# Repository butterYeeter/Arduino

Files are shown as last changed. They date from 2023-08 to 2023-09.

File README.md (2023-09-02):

# Robot Documentation

<!-- > Disclaimer! This repo is a fork of the actual repo used so that we could format it nicely -->

## Table of Contents
- [Performance Video](#performance-video)
- [Mobility Management](#mobility-management)
  - [Robot Version 1](#robot-version-1)
  - [Improvements](#improvements)
- [Power and Sense Management](#power-and-sense-management)
  - [Robot Version 1](#robot-version-1-1)
  - [Improvements](#improvements-1)
- [Obstacle Management](#obstacle-management)

### Performance Video
https://github.com/butterYeeter/Arduino/assets/100842250/680a6417-5dfc-4aaf-9352-56b448d2d792

### Mobility Management
#### Robot Version 1
In the first version of the **'robot'**, the **motors were managed by an [Arduino Nano](/docs/nano.pdf)**. We **communicated with board via [I2C](https://en.wikipedia.org/wiki/I%C2%B2C)**. The main board(a [Pi Pico](/docs/pico.pdf)) sent what speed the motors should be run. The **motor speed was controlled via [PWM](https://en.wikipedia.org/wiki/Pulse-width_modulation)**. High torque low rpm motors were used in the beginning however we ran into issues with the complicated belt system used to drive the wheels. 
 
We then **switched to a lower torque but high rpm brushed dc motor** which was **compatible with an 'off the shelf' gear box**. The motor was also run at a higher than recomended voltage and was **wired with capicitors to reduce EMF**(Which was causing our gyro control board to reset). Steering was handled using another **pi pico with a gyro sensor attached**. This board **controlled a servo using PWM** which controlled the steering rack. The main board communicated(via I2C) the target angle the gyro board should maintain using the steering rack.

The **old chasis** was a combination of 3D printing and hand cut MDF board. The model was a modification(done in Fusion 360) of a base design provided to us by our club. All the control boards as well as the the motor, gear box, servo, gyro, battery and boost converters were **mounted to this chasis**. The TOF sensors used for naviation were mounted to an **mdf frame**(which was connected to the chasis). [Model available here](https://github.com/butterYeeter/Arduino/blob/main/models/body_v2.stl)

<p>
    The drive motor
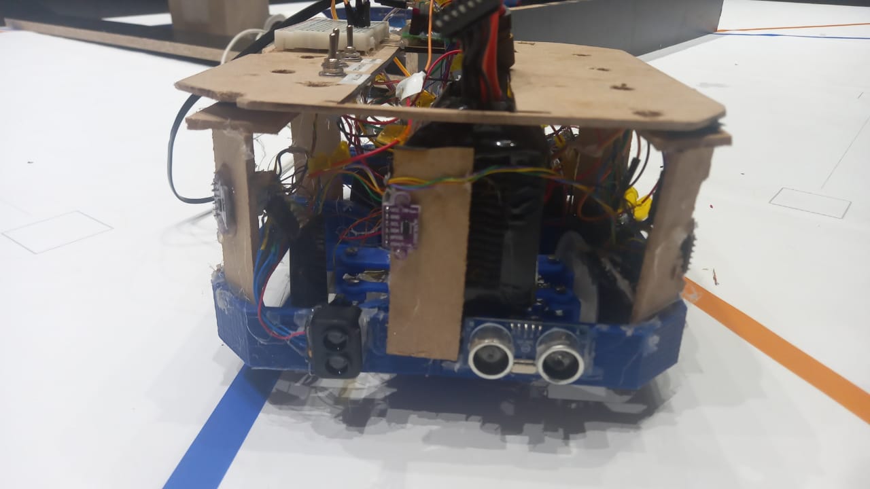
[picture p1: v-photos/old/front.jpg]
Meet Chihuahua! Our lovely, crazy robot :P
    
</p>

#### Improvements
After the provintial round of the competition, a major decision was made to completely redesign the robot. A new chasis was designed(available ```[here](/models/body_v2.stl)```) and is **completely 3D printed**. This helped improve on the flimsy nature of the old MDF frame. **Components** of the old design was **reused** such as the servo for steering as well as the gearbox. The chasis consists of an **interior chasis for mounting components**, steering rack and motors and an **exterior chasis that acts as a bumper**. 

A choice was made to use **2 drive motors**(connected to the same axle) for **increased torque**(initially a decision was made to ram into the walls according to which traffic sign is seen by the camera). Previously **8 [Time of Flight](/docs/tof.pdf) sensors was used** however we then **switched to one fancy 360 degrees scanning lidar**. This is mounted in the center of the chasis and **no other components sit above it to prevent inteference with the measurements**. On top of the lidar, a **```pixy cam``` is mounted on a servo to scan for traffic signs**.

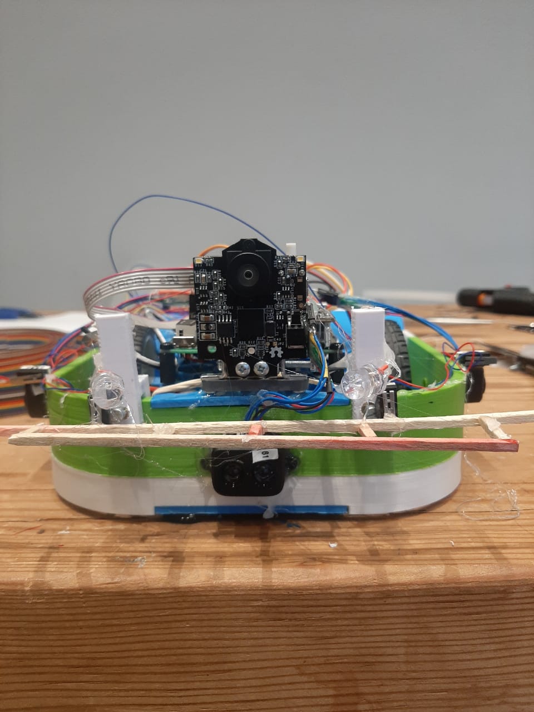
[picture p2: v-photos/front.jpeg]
Meet chihuahua mk3


### Power and Sense Management
#### Robot Version 1
The first version of the robot was **powered** using a **3 cell Li-PO battery** however we ran into **issues**. We then **tested using a 2 cell Li-PO** however the **voltage drop** was too great and their were **capacity issues**.  We ulitmately switched to a **6 cell battery in combination with voltage regulators**. 

A variety of sensors were used in this first robot for the challenges. 8 **[Time of Flight](/docs/tof.pdf)** sensors(and one fancy one) as well as a **[BMP 180](/docs/bmp180.pdf)**(the old gyro). These were **managed by 2 [Rasberry Pi Pico's](/docs/pico.pdf)**, one for managing the Time of Flight sensors and one for managing the gyro(BMP 180). The **time of flight sensors detected the distance from the walls** from all sides of the car. The **main board would then request the sensor data** from the Time of Flight board. The gyro board simply used the **BMP 180's output for driving straight** consistently and would accept a **target angle to follow from the main board**.

#### Improvements
The new robot is **powered by a 4 cell battery due to new the chasis**. The previous **6 cell would not fit** within the allocated space on the chasis so we used the **smaller 4 cell**. The 8 time of flight sensors as well as the one fancy time of flight were **discarded in favour of a 360 degree scanning lidar**. The old sensors had a bad field of view and would throw false positives as to what the actual distance reading was. This caused major issues when it came to reliablity of the function of the car. The new lidar has an **excellent field of view of just 2 degrees** and can measure distances of up to 12 meters. This has greatly reduced errors that were associated to the time of flight sensors. We still use a **Pi Pico for managing** this sensor. The sensor uses a basic **one wire serial interface**. Unfortunately there were further issues with dynamic memory allocation as we had to port a library from the Raspberry Pi 4B to the Pi Pico. We finally on 3 good time of flight sensor which are reliable. 

<p align=center>
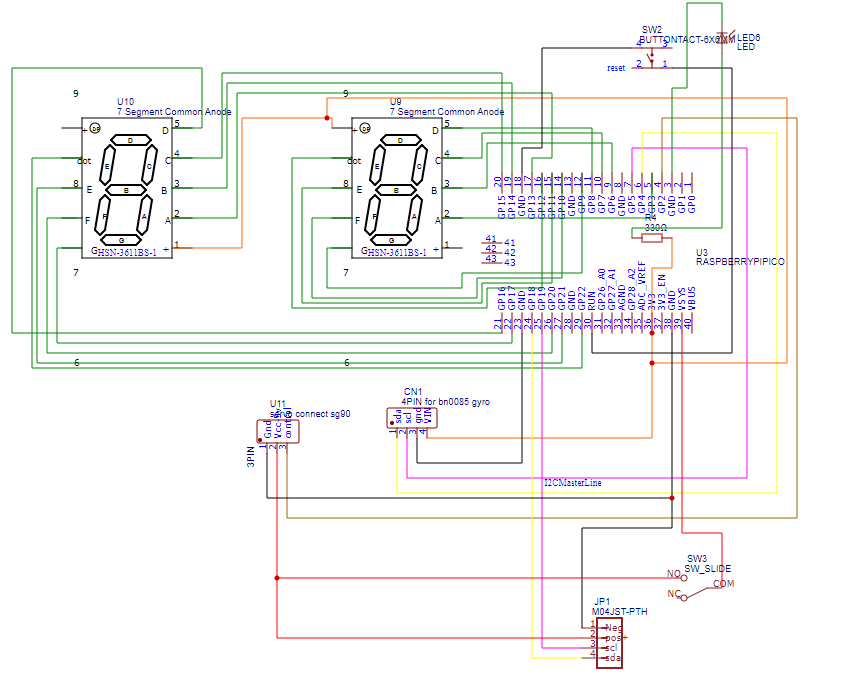
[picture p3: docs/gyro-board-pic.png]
Main Board and LIDAR
  
</p>
<p align=center>
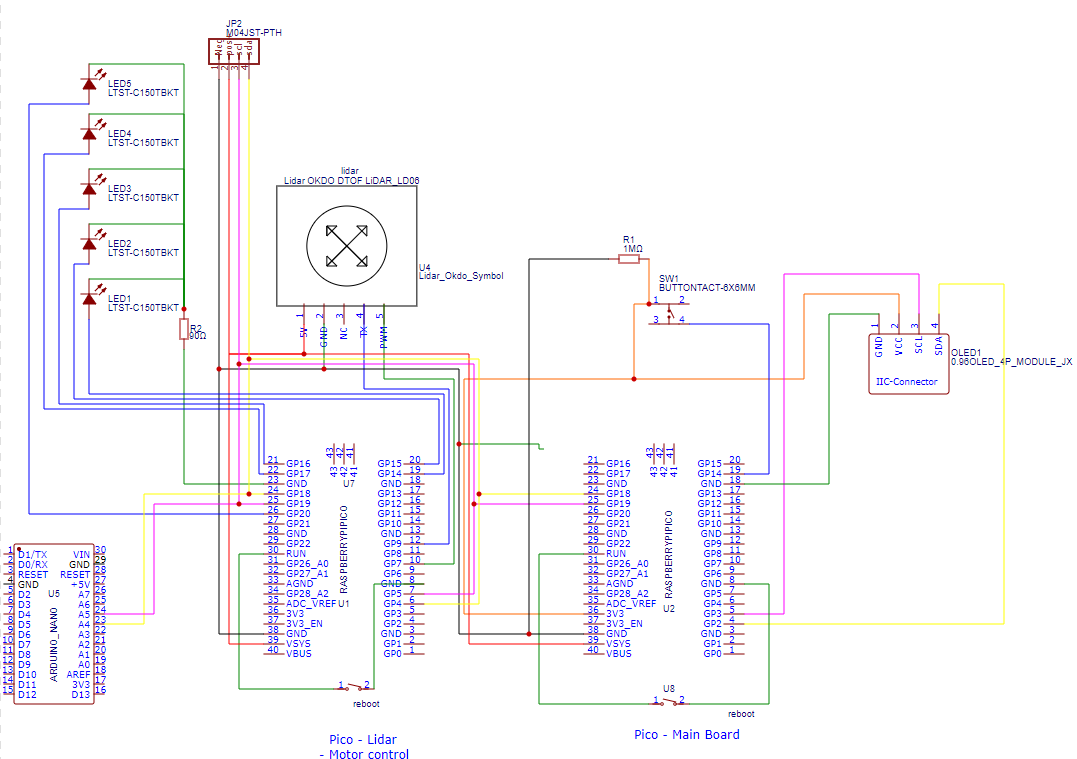
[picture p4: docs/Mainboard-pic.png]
Gyro Board
  
</p>

Another **issue** we had was **with the old gyro sensor**. Under certain conditions(erratic movement when following a target angle) the **gyro would drift** away from the true angle. This was another major issue that we addressed. We have since **switched to an absolute position sensor**. It is called the **BNO085** which has an **accelerometer, gyrometer and magnotometer**. Through the dark arts of sensor fusion, **gyro drift has been erradicated**. This sensor is managed by its a Pi Pico as well.

### Obstacle Management
For the **open round** the robot **simply uses 2 time of flight sensors** on the left and right of the car and **one gyro**. The gyro **is used to maintain a straight line** while driving as well as **steering** around corners. The **time of flight sensors are used to detect when a wall falls away**(the distance measurement suddenly increases). This can **tell us whether to go clockwise or anti-clockwise** automatically.

<p align=left>The BNO085</p>

For the challenge round the **previous sensors are used in addition to a pixy cam v2**. The pixy cam is **configured to detect the signitures of the traffic signs** and **communicates over I2C whether to go left, right on stay in the middle**(aka no block in the section). When a **signiture is detected** the main board sends a **new target to the gyro board** and **slows down the motor board**.  This is done so that the **robot can 'hug' the correct wall before it passes the traffic sign**. 

```mermaid
---
title: Logic Flow for Open Round
---
flowchart TD
    start([Start])
    move1[Drive forward]
    move2[Drive forward]
    wall{Has wall fallen away?}
    angle1[Set new target angle]
    steer1[Steer to new target angle]
    numturn1[Number of turns = 0]
    numturn2[Number of turns + 1]
    numturns{Have we done 12 turns?}
    finalsection[Stop in final section]
    ending([End])
    start-->numturn1-->move1-->wall-- no -->move2
    wall-- yes -->angle1-->steer1-->numturn2-->numturns-- no -->move1
    move2-->wall
    numturns-- yes -->finalsection-->ending
```

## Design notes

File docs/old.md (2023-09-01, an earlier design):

# Robot Documentation
<p align=center>
Meet Chihuahua! Our lovely, crazy robot :P
</p>

## <u>**Table of Contents**</u>
- [History](#history)
- [Parts](#parts)
- [Board-Details](#board-communication)
- [Parts Design](#parts-design)
- [Management](#management)
  - [Mobility](#mobility)
  - [Power-and-Sensors](#power-and-sensors)
  - [Obstacle-Avoidance](#obstacle-avoidance)
- [Software Implementation](#software-implementation)
  - [Global Variables](#global-variables)
  - [Macro Definitions](#macro-definitions)
  - [Modules](#modules)

## [**History**](/docs/history.md#history)
Firstly we started this project by splitting our efforts and worked on both an arduino based robot and an ev3 based robot. Due to school restricting the time we had to work on both, more progress was made on the arduino based robot and it was decided to use this for the competition.
More info [here](/docs/history.md)

## [**Parts**](/docs/parts.md)

<details open>

<summary>List of all the parts</summary>

 - 2x Raspberry Pi Pico
 - 1x Arduino nano
 - 1x Breadboard
 - 3x Prototyping board
 - 2x Voltmeter
 - 3x Buck convertor
 - 3x Switches
 - 1x 6s 1500mah batteries
 - 8x TOF sensors
 - 1X Luna TOF sensor
 - 1x Ultrasonic sensor
 - 1x Servo motor
 - 1x 6v DC motor
 - 1x Gearbox
 - 1x Capacitor (40V 300mF)
 - 1x Barrel conector
 - 1x BMI 180 Gyro
 - 2X Common anode 7 segment display
 - 1x Motor Driver
 - 1x ESP32 Cam
 - LEDS
 - Wrapping Wire
 - Wheels
 - Jumpers

</details>

 More info can be found [here](/docs/parts.md)

## **Board Communication**

It is quite a lengthy parts list however we believe all the components are vital. We have 4 microtrollers each serving specific and important functionality. The functions are as follows: 
- Camera(ESP 32) board - handles positioning via video. sends data to the TOF board
<p align=left>
Picture of ESP32 camera board
</p>

- Gyro(Pi Pico) board - relative gyro, calculates angle for turning
- TOF(Pi Pico) board - Master I2C board. Does all the distance measuring and logic
<p align=left>
A Raspberry Pi Pico is used for both the TOF board and Gyro board
</p>

- Motor Control board - Controls the drive motor via PWM and controls servo for steering

<p>
Arduino Nano receives commands for the other boards for steering and driving
</p>

The boards all communicate via the I2C protocol.

## **Parts Design**
This section is to document the design on the mdf board parts and 3D printed chasis. The mdf board parts were designed and cut by hand. The 3D printed chasis and steering components were designed int Fusion 360 and made on Michael's printer. There are some bolts to hold the steering rack together and hot glue to hold the various electronics to the chasis. 3D model of chasis [here](/models/body_v2.stl)

<p>
Hot glue mess
</p>

## **Management**
 We will now discuss specific management of mobility, power, sensor and obstacle management.

### *Mobility*
Mobility: Initially a high torque low RPM motor was used, but the complicated belt system made this impractical. We then switched to a lower torque but much higher speed motor that was compatible with an off the shelf gearbox, this is what we are currently using. ```Mention the encoded and non-encoded motors.``` The current motor is also run at a higher voltage than is supposed to and is wired with capacitors to reduce EMF which was interfering with our gyro board causing it to reset.

### *Power and sensors*
Initialy powered off of a 3s Li-ion battery however the voltage was too high. We then switched to a 2s Li-ion battery however the voltage drop was too great and there was capacity issues. We found it easier to switch to a 6 cell drone battery and use multiple voltage regulators. This is what worked best for us and what is currently in use.

### *Obstacle avoidance*
Through the series of 8 short range time of flight sensors and one long range one (only one was used to high cost) we created what is essentialy poor man's LIDAR. We then only track the inside walls as we found it the simplest solution for position and owrks best with the short range TOF sensor array. The robot aims to drive between 100 and 300mm away from the inside wall. When the robot no longer detects the inside wall it knows that it should turn. As for the obstacle chanllenge the robot makes use of the camera and TOF array to determine the position of the robot relative to the obstacle as well as the color of the obstacle. It will then hug one of side walls depending on wether is a red or green obstacle.

This documentation provides an in-depth understanding of our robot's design, components, and operational principles. We have had fun working on these robots and hope to pass through to nationals. I actually had a lot of fun write the Markdown for this doc lol.

## **Software Implementation**
### *Global Variables*
```C
TFLI2C tflI2C;

int16_t tfAddr = TFL_DEF_ADR;    // default I2C address
uint16_t tfFrame = TFL_DEF_FPS;  // default frame rate

int16_t tfDist = 0;  // distance in centimeters
int16_t tfFlux = 0;  // signal quality
int16_t tfTemp = 0;  // temperature in 0.01 degree Celsius

// other device variables
uint16_t tfTime = 0;  // devie clock in milliseconds
uint8_t tfVer[3];     // device version number
uint8_t tfCode[14];   // device serial number

const short int serialAdress = 3;

//ControlPins
const int frontPin = 15;
const int Right45Pin = 12;
const int frontRightPin = 11;
const int Left45Pin = 14;
const int frontLeftPin = 13;
const int backRightPin = 10;
const int backLeftPin = 9;
const int backPin = 16;

//Create the sensor objects
Adafruit_VL53L0X front = Adafruit_VL53L0X();
Adafruit_VL53L0X right45 = Adafruit_VL53L0X();
Adafruit_VL53L0X frontRight = Adafruit_VL53L0X();
Adafruit_VL53L0X left45 = Adafruit_VL53L0X();
Adafruit_VL53L0X frontLeft = Adafruit_VL53L0X();
Adafruit_VL53L0X backRight = Adafruit_VL53L0X();
Adafruit_VL53L0X backLeft = Adafruit_VL53L0X();
Adafruit_VL53L0X back = Adafruit_VL53L0X();

//Create the RanginemeasurementData object to hold the measurement data
VL53L0X_RangingMeasurementData_t frontMeas;
VL53L0X_RangingMeasurementData_t right45Meas;
VL53L0X_RangingMeasurementData_t frontRightMeas;
VL53L0X_RangingMeasurementData_t left45Meas;
VL53L0X_RangingMeasurementData_t frontLeftMeas;
VL53L0X_RangingMeasurementData_t backRightMeas;
VL53L0X_RangingMeasurementData_t backLeftMeas;
VL53L0X_RangingMeasurementData_t backMeas;

//IndicatorLED constants
const int redLED = 6;
const int greenLED = 7;
const int blueLED = 8;

// Global variables for keeping all the distance values from the 8 short range TOF sensors
int frontVal;
int right45Val;
int frontRightVal;
int left45Val;
int frontLeftVal;
int backRightVal;
int backLeftVal;
int backVal;

const int echoPin = 27;
const int trigPin = 26;

const float pi = 3.14159265358979; // Constant float for PI

bool turningRight; // Is the robot turning right

int8_t motorState = 0;
int targetAngle = 0;    // Angle that the robot should currently be parallel with.

int wallNum = 1;    // To keep track of number of times the robot has gone around the track

// Series of variables for help in positioning
int firstWallDist = -1; 
int secondWallDist = -1;
int thirdWallDist = -1;
int fourthWallDist = -1;

int deg90 = 90;
int turnOffset = 5;
```

### *Macro Definitions*
```C
// I2C addresses of the TOF sensors
#define LOX1_ADDRESS 0x30
#define LOX2_ADDRESS 0x31
#define LOX3_ADDRESS 0x32
#define LOX4_ADDRESS 0x33
#define LOX5_ADDRESS 0x34
#define LOX6_ADDRESS 0x35
#define LOX7_ADDRESS 0x36
#define LOX8_ADDRESS 0x37
```

### *Modules*
```C
void lookAtSide();

// Function which makes the robot follow along the inner wall
void alongWall();

// void *movement() functions records important data in the first lap for later use.
void firstmovement();
void secondMovement();
void thirdMovement();
void firstmovement();

// void readAll() receives distance data from all the TOF sensors
void readAll();

// setMotor(int8_t  motorNum) sets the speed of the drive motor
void setMotor(int8_t motorNum);

//  read angle returns the current angle of the robot as an int
int readAngle();
// Sets the current target angle to folow
void setAngle(int targetAngle);

// Reads gyro data of I2C and receives the rate of rotation
int checkGyro();

// This function checks the serial bus for any important data
int checkSerial();

// send*(int sendInt) functions split the 16 bit integer into 2 bytes and send them over serial and I2C protocols respectively
void sendInt(int sendInt);
void sendWireInt(int sendInt);
// Inverse of the send*() functions. Just receive a 16 bit int over serial and I2C respectively
int recieveInt();
int recieveWireInt();

// Halts execution until a target turn is complete
void waitForTurn();

// int read*() functions just read distance data from a specified TOF sensor using the appropriate postfix after read. Data returned as an int. These functions exist because reading data from all the TOF sensors at once is too slow
int readFront();
int readRight45();
int readFrontRight();
int readLeft45();
int readLeft45();
int readBackLeft();
int readBackRight();
int readBack();

// This funciton just setups all the TOF sensors and specifies their individual I2C addresses
void setUpSensors();

// This utility function displays custom error codes through the indicator LED's that are part of the robot. Extremely useful for debugging and better than Serial monitor because Serial.println is really slow
void setUpFailedError(int code);

// This boots up the fancy Luna TOF and does a self check.
void bootTFLuna(uint8_t adr);

// This reads data from the fancy TOF and returns it as an int.
int getLIDAR();

// Displays all the distance data from the 8 short range TOF sensors in the Serial Monitor.
void displayAllDistances();
```

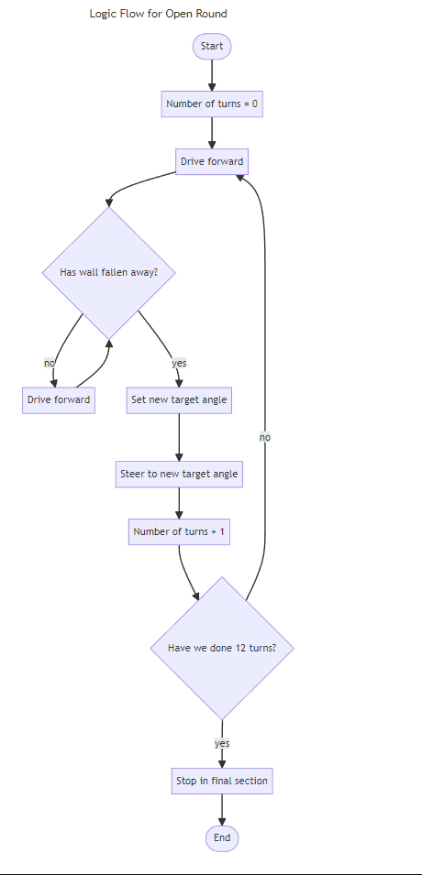
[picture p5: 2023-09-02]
docs/flowchart.png

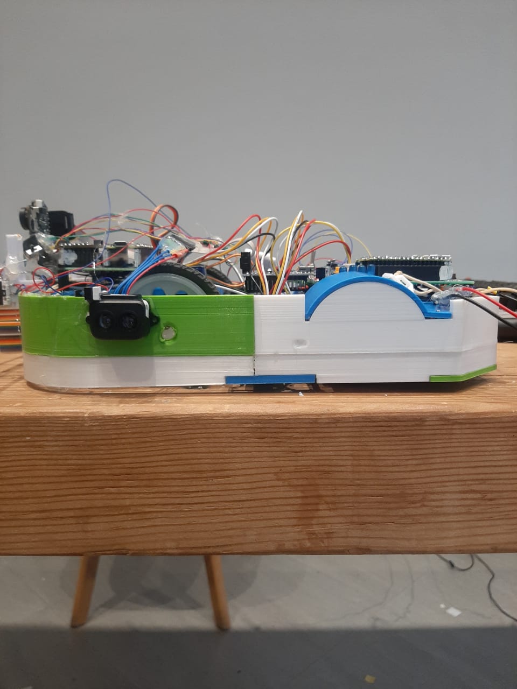
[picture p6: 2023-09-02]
v-photos/left.jpeg

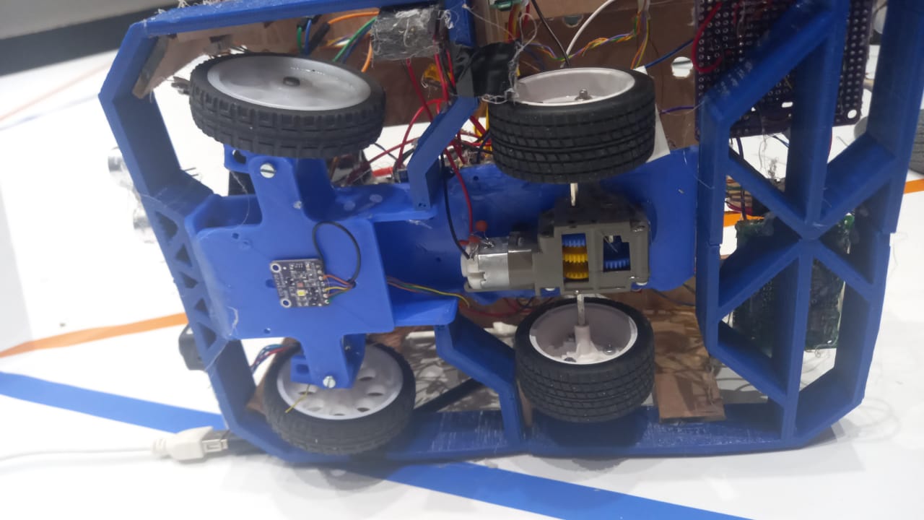
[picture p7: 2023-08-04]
v-photos/bottom.jpg

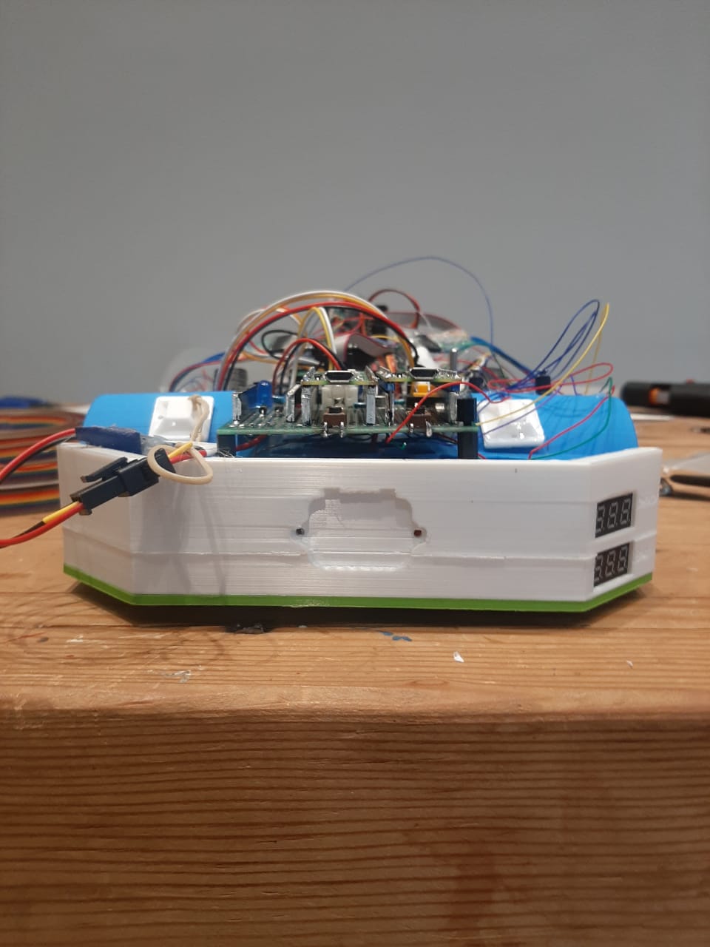
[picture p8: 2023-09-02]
v-photos/back.jpeg

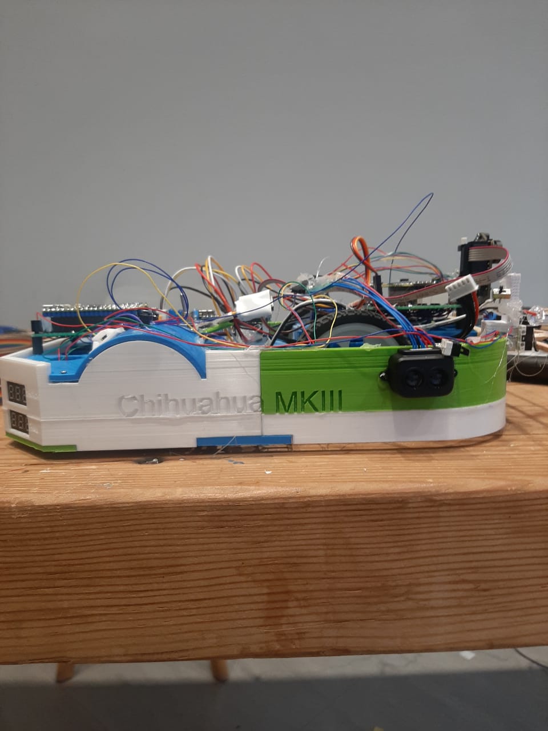
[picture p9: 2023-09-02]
v-photos/right.jpeg

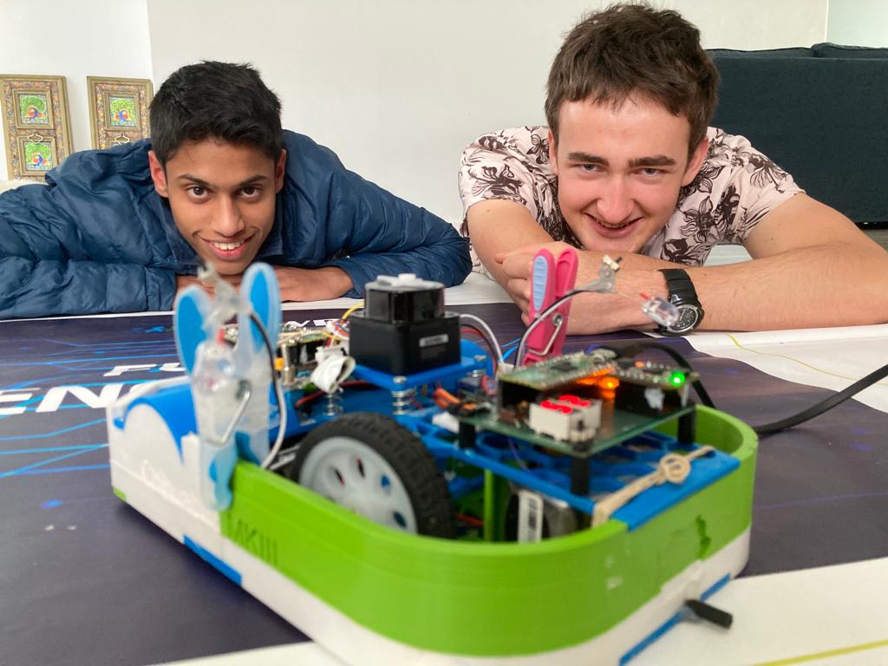
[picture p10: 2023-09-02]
t-photos/team_photo_2.jpg

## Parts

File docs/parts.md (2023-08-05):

# Parts Documentation

The robot is built on a 3D printed chasis designed by a member of the team. All components are fitted to this chasis. The parts list include the following:
- 2x [Raspberry Pi Pico](#pi-pico)
- 1x [Arduino nano](#arduino-nano)
- 1x Breadboard
- 3x Prototyping board
- 2x Voltmeter
- 3x Buck convertor
- 3x Switches
- 1x 6s 1500mah batteries
- 8x [TOF sensors](#time-of-flight-sensors)
- 1X [Luna TOF sensor](#time-of-flight-sensors)
- 1x Ultrasonic sensor
- 1x Servo motor
- 1x 6v DC motor
- 1x Gearbox
- 1x Capacitor (40V 300mF)
- 1x Barrel conector
- 1x [BMP 180 Gyro](#bmp-180)
- 2X Common anode 7 segment display
- 1x Motor Driver
- 1x [ESP32 Cam](#esp-32-cam)
- LEDS
- Wrapping Wire
- Wheels
- Jumpers

## Pi Pico
The Raspberry Pi Pico is a powerful dual core micro controller that runs at 160 MHz. We chose this board due to its cheap price and processing power which is able to keep up with our requirements. Docs [here](/docs/pico.pdf) (See page 17 and 24 for brief usage info)

## Arduino Nano
The Nano is a cheap small sbc that runs at 16 MHz. Initially our robot Chihuahua used 3 of these for sensor, motor and gyro management, however it lacked the processing power for the latter 2 functions. The motor control board is still a nano to this day as it is a basic task. Docs [here](/docs/nano.pdf) (See page 8)

## Time Of Flight Sensors
Time of flight sensors work by sending out a laser signal and measuring the time it takes to come back. We use an array of these for our positioning system. However due to the high costs of long range sensors we mainly use short range ones which are adequate. Data sheet [here](/docs/tof.pdf) (See page 16 for Control Interface info)

## BMP 180
Our dear gyro who we have to thank for steering. It works in combination with the TOF sensors to maintain the robots position and also is required for accurate turning. Data sheet [here](/docs/bmp180.pdf)

## Esp 32 cam
This board helps us to figure out the positions of obstacles. The obstacle avoidance is still in progress. The camera runs at a fairly low resolution as the Esp32 has trouble processing high resolution(Quite shocking just how demanding video is.) Which allows it to run at a decent fps. Due to issues the obstacle challenge isn't our main focus. More info on the board [here](/docs/esp32cam.pdf) These docs aren't for our board but Esp32 camera boards are quite generic so this doc is fine.

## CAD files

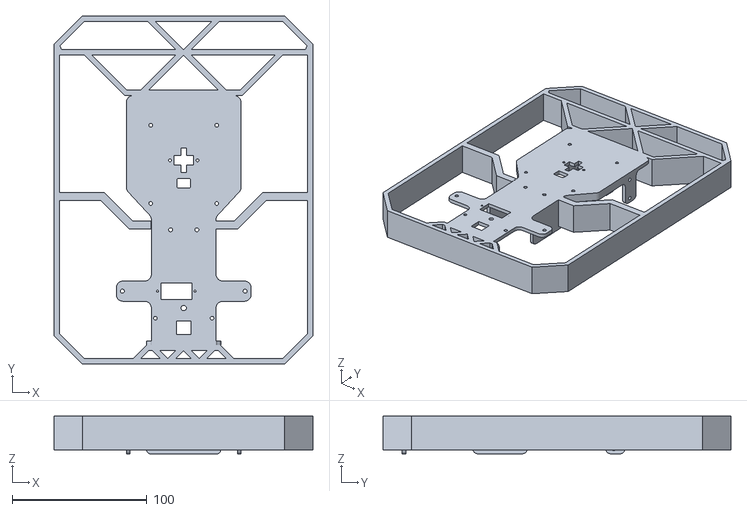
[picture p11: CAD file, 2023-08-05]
models/body_v2.stl
192.0 x 258.0 x 28.0

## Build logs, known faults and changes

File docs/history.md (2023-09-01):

# <u>**History**</u>
Progress was slow during the beginning of the year. We didn't have a mat to practice on so while we waited for our coach to get one we slowly built our robots. 

We did get a mat however school got quite busy this year with both of use being in the senior grades. We both just started with experimenting with our respective platforms(Michael worked on the Arduino bot while I used EV3). The EV3 is still incomplete however Michael's bot shows promise. There were a few mishaps like the motor driver board dying. Initially Michael used 3 [Arduino Nanos](/docs/parts.md#arduino-nano) as our control and logic boards however they did not meet the processing requirements. Later on an [Esp 32 camera](/docs/parts.md#esp-32-cam) board was added for the obstacle challenge. At some point our gyro board(Which we changed to a [Pi Pico](/docs/parts.md#pi-pico)) died and had to be replaced. There was also issues with powering the robot from the initial 3 cell Li-ion battery. Currently we use a 6 cell battery with voltage regulators. We had fun and hope to score well as we only have 1 and 2 chances to enter into WRO competitions in the future. 

the address of the motor board is 13.
lidar is 11
gyro is 12

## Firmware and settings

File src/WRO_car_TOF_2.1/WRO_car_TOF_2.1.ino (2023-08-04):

#include <Wire.h>

#include "Adafruit_VL53L0X.h"
#include <SoftwareSerial.h>


SoftwareSerial TOFBus(17, 18);  // RX, TX

//sensor addresses
#define LOX1_ADDRESS 0x30
#define LOX2_ADDRESS 0x31
#define LOX3_ADDRESS 0x32
#define LOX4_ADDRESS 0x33
#define LOX5_ADDRESS 0x34
#define LOX6_ADDRESS 0x35
#define LOX7_ADDRESS 0x36
#define LOX8_ADDRESS 0x37

const short int serialAdress = 3;

//ControlPins
const int frontPin = 15;
const int Right45Pin = 12;
const int frontRightPin = 11;
const int Left45Pin = 14;
const int frontLeftPin = 13;
const int backRightPin = 10;
const int backLeftPin = 9;
const int backPin = 16;

//Create the sensor objects
Adafruit_VL53L0X front = Adafruit_VL53L0X();
Adafruit_VL53L0X right45 = Adafruit_VL53L0X();
Adafruit_VL53L0X frontRight = Adafruit_VL53L0X();
Adafruit_VL53L0X left45 = Adafruit_VL53L0X();
Adafruit_VL53L0X frontLeft = Adafruit_VL53L0X();
Adafruit_VL53L0X backRight = Adafruit_VL53L0X();
Adafruit_VL53L0X backLeft = Adafruit_VL53L0X();
Adafruit_VL53L0X back = Adafruit_VL53L0X();



//Create the RanginemeasurementData object to hold the measurement data
VL53L0X_RangingMeasurementData_t frontMeas;
VL53L0X_RangingMeasurementData_t right45Meas;
VL53L0X_RangingMeasurementData_t frontRightMeas;
VL53L0X_RangingMeasurementData_t left45Meas;
VL53L0X_RangingMeasurementData_t frontLeftMeas;
VL53L0X_RangingMeasurementData_t backRightMeas;
VL53L0X_RangingMeasurementData_t backLeftMeas;
VL53L0X_RangingMeasurementData_t backMeas;


//IndicatorLED constants
const int redLED = 6;
const int greenLED = 7;
const int blueLED = 8;

int frontVal;
int right45Val;
int frontRightVal;
int left45Val;
int frontLeftVal;
int backRightVal;
int backLeftVal;
int backVal;

const int echoPin = 27;
const int trigPin = 26;

const float pi = 3.14159;


bool turningRight;

int8_t motorState = 0;
int targetAngle = 0;

bool oddWall = false;

int oddWalldist = -1;
int evenWalldist = -1;


int turnOffset = 0;
void setup() {

  TOFBus.begin(57600);
  Serial.begin(9600);

  Wire.begin();
  Wire.setClock(100000);

  Wire1.setSDA(18);
  Wire1.setSCL(19);
  Wire1.begin();

  pinMode(25, OUTPUT);
  pinMode(redLED, OUTPUT);
  pinMode(blueLED, OUTPUT);
  pinMode(greenLED, OUTPUT);



  pinMode(frontPin, OUTPUT);
  pinMode(Right45Pin, OUTPUT);
  pinMode(frontRightPin, OUTPUT);
  pinMode(Left45Pin, OUTPUT);
  pinMode(frontLeftPin, OUTPUT);
  pinMode(backRightPin, OUTPUT);
  pinMode(backLeftPin, OUTPUT);
  pinMode(backPin, OUTPUT);

  pinMode(trigPin, OUTPUT);
  pinMode(echoPin, INPUT);

  digitalWrite(redLED, LOW);
  digitalWrite(blueLED, LOW);
  digitalWrite(greenLED, LOW);

  for (int i = 0; i < 3; i++) {
    Serial.println("Flash");
    digitalWrite(redLED, HIGH);
    delay(100);
    digitalWrite(redLED, LOW);

    digitalWrite(blueLED, HIGH);
    delay(100);
    digitalWrite(blueLED, LOW);

    digitalWrite(greenLED, HIGH);
    delay(100);
    digitalWrite(greenLED, LOW);
    delay(300);
  }

  // wait until serial port opens for native USB devices
  //while (! Serial) {
  digitalWrite(25, HIGH);
  delay(100);
  digitalWrite(25, LOW);
  delay(100);
  // }

  Serial.println("Adafruit VL53L0X test");

  setUpSensors();
  // power
  Serial.println(F("VL53L0X API Simple Ranging example\n\n"));


  readAll();
}


void loop() {

  setMotor(6);

  firstmovement();
  setMotor(10);
  oddWall = true;


  //delay(1000);

  
    secondMovement();
    setMotor(10);

  while (true) {
    alongWall();
    setMotor(10);
    delay(300);
    // setAngle(targetAngle);
  }

  


  Serial.print(frontVal);
  Serial.print("  |  ");

  Serial.print(right45Val);
  Serial.print("  |  ");
  Serial.print(frontRightVal);
  Serial.print("  |  ");
  Serial.print(left45Val);
  Serial.print("  |  ");
  Serial.print(frontLeftVal);
  Serial.print("  |  ");
  Serial.print(backRightVal);
  Serial.print("  |  ");
  Serial.print(backLeftVal);
  Serial.print("  |  ");
  Serial.print(backVal);
  Serial.println("");
  //int request =
  /*
  setAngle(-90);

  //delay(100);
  Serial.print("\t\t\t\t\t\t\t\t\t\t\t Checking GYRO: ");
  Serial.println(checkGyro());*/
}


void alongWall() {

  bool edgeFound = false;


  int forward, front, back;
  int turnDelay = 0;
  int targetAngleOfset = 0;
  int angleAjustment = 15;

int counter= 0;


  if (turningRight) {



    bool waiting = true;
    int counter = 0;
    while (waiting) {
      int distance = readFrontRight();
      Serial.println(distance);
      if (distance != -1) {
        counter++;
      } else {
        counter = 0;
      }
      Serial.println("Waiting right");
      delay(10);
      if (counter == 5) {

        setMotor(6);
        waiting = false;
      }
    }


  } else {

    bool waiting = true;
    int counter = 0;
    while (waiting) {
      int distance = readFrontLeft();
      Serial.println(distance);
      if (distance != -1) {
        counter++;
      } else {
        counter = 0;
      }
      Serial.println("Waiting Left");
      delay(10);
      if (counter == 5) {

        setMotor(6);
        waiting = false;
      }
    }
    
  }


  while (!edgeFound) {
    setAngle(targetAngle + targetAngleOfset);

    if (turningRight) {
      frontVal = readFront();
      frontRightVal = readFrontRight();
      backRightVal = readBackRight();

      forward = frontVal;
      front = frontRightVal;
      back = backRightVal;

    } else {
      frontVal = readFront();
      frontLeftVal = readFrontLeft();
      backLeftVal = readBackLeft();
      forward = frontVal;
      front = frontLeftVal;
      back = backLeftVal;
    }

    float distMultiplier = cos(targetAngleOfset * pi / 180);

    int estDist = distMultiplier * (front + back) / 2;

    int ultraSonicDist = getUltrasonic();
    Serial.print("\t\t\t\t front = ");
    Serial.print(forward);
    Serial.print("\t");
    Serial.print(ultraSonicDist);
    Serial.print(" / ");

    if(oddWall){
Serial.print(oddWalldist);
    }else{
      Serial.print(evenWalldist);
    }
    Serial.print("\t\t front side = ");
    Serial.print(front);
    Serial.print("\t\t back side =");
    Serial.print(back);
    Serial.print("\t\t");
    Serial.print(targetAngle + targetAngleOfset);


    Serial.print("\t\t\t\tEstimated Distance:");
    Serial.println(estDist);





    if (estDist > 300) {
      Serial.println("Going closer to the wall");
      if (turningRight) {
        targetAngleOfset = angleAjustment;
      } else {
        targetAngleOfset = -angleAjustment;
      }

      delay(turnDelay);

    } else if (estDist < 50) {
      Serial.println("Moving further away from the wall");
      if (turningRight) {
        targetAngleOfset = -angleAjustment;
      } else {
        targetAngleOfset = +angleAjustment;
      }

      delay(turnDelay);

    }

    else if (estDist > 80 || estDist < 120) {
      Serial.println("Correct distance to the walll");
      targetAngleOfset = 0;
      delay(turnDelay);

    } else {
      Serial.println("Somthing about a wall");
    }

    
    if(oddWall){
    if(ultraSonicDist < oddWalldist){
      oddWall = false;
      counter++;
    }  
    }else{

      if(ultraSonicDist < evenWalldist){
oddWall = true;
        counter++;
    } 
    }

    if(counter == 3){
      edgeFound = true;
    }
  }

  
  if (turningRight) {
    Serial.println("--------Turning Right--------");
    targetAngle += 92;
    setAngle(targetAngle);
  } else {
    Serial.println("--------Turning Left--------");
    targetAngle -= 92;
    setAngle(targetAngle);
  }





}





void firstmovement() {
  setAngle(0);



  bool edgeFound = false;


  while (!edgeFound) {

    frontRightVal = readFrontRight();
    frontLeftVal = readFrontLeft();

    Serial.print(frontLeftVal);
    Serial.print(" \t\t\t\t | \t\t\t\t ");
    Serial.println(frontRightVal);



    if (frontRightVal == -1) {
      turningRight = true;
      edgeFound = true;
    } else if (frontLeftVal == -1) {
      turningRight = false;
      edgeFound = true;
    }
  }
  if (turningRight) {
    Serial.println("--------Turning Right--------");
    setAngle(90);
    targetAngle = 90;
  } else {
    Serial.println("--------Turning Left--------");
    setAngle(-90);
    targetAngle = -90;
  }


  oddWalldist = getUltrasonic();
  Serial.println("--------Ultrasonic dist--------");
  Serial.println(oddWalldist);
}



void secondMovement() {

  bool edgeFound = false;





  if (turningRight) {



    bool waiting = true;
    int counter = 0;
    while (waiting) {
      int distance = readFrontRight();
      Serial.println(distance);
      if (distance != -1) {
        counter++;
      } else {
        counter = 0;
      }
      Serial.println("Waiting right");
      delay(50);
      if (counter == 5) {

        setMotor(6);
        waiting = false;
      }
    }

    while (!edgeFound) {

      frontRightVal = readFrontRight();

      Serial.println(frontRightVal);



      if (frontRightVal == -1) {
        turningRight = true;
        edgeFound = true;
      }
    }

  } else {

    bool waiting = true;
    int counter = 0;
    while (waiting) {
      int distance = readFrontLeft();
      Serial.println(distance);
      if (distance != -1) {
        counter++;
      } else {
        counter = 0;
      }
      Serial.println("Waiting Left");
      delay(50);
      if (counter == 5) {

        setMotor(6);
        waiting = false;
      }
    }
    while (!edgeFound) {


      frontLeftVal = readFrontLeft();

      Serial.println(frontLeftVal);




      if (frontLeftVal == -1) {
        turningRight = false;
        edgeFound = true;
      }
    }
  }


  if (turningRight) {
    Serial.println("--------Turning Right--------");
    targetAngle += 92;
    setAngle(targetAngle);
  } else {
    Serial.println("--------Turning Left--------");
    targetAngle -= 92;
    setAngle(targetAngle);
  }







  evenWalldist = getUltrasonic();
}

void readAll() {

  right45Val = readRight45();
  left45Val = readLeft45();
  frontVal = readFront();
  frontRightVal = readFrontRight();
  frontLeftVal = readFrontLeft();
  backRightVal = readBackRight();
  backLeftVal = readBackLeft();
  backVal = readBack();
}


void setMotor(int8_t motorNum) {
  Serial.println("Transmitting Wire");
  Wire1.beginTransmission(13);


  byte motorState = motorNum;
  Wire1.write(motorState);


  Wire1.endTransmission();
}

int readAngle(){
Wire1.requestFrom(12, 2);
int16_t currentAngleTMP = readWireInt();
return currentAngleTMP;

}

void setAngle(int targetAngle) {
  Serial.println("Transmitting Wire");
  Wire1.beginTransmission(12);

  sendWireInt(targetAngle);

  Wire1.write(motorState);


  Wire1.endTransmission();
}

int checkGyro() {
  // Serial.println("Checking Gyro");
  digitalWrite(13, HIGH);

  //delay(50);


  Wire1.requestFrom(12, 2);

  int returnInt = recieveWireInt();



  //delay(50);
  return returnInt;
  //delay(50);
  // digitalWrite(13, LOW);
}




int checkSerial() {
  Serial.println("Checking Serial");
  if (TOFBus.available() > 0) {
    Serial.println("SERIAL FOUND");
    digitalWrite(redLED, HIGH);
    digitalWrite(blueLED, HIGH);
    digitalWrite(greenLED, HIGH);
    digitalWrite(25, HIGH);
    //dataPackets = "<3><120>";
    byte request = TOFBus.read();
    Serial.println(request);
    if (request == 0) {
      sendInt(frontVal);



    } else if (request == 1) {
      sendInt(right45Val);
    } else if (request == 2) {
      sendInt(frontRightVal);
    } else if (request == 3) {
      sendInt(left45Val);
    } else if (request == 4) {
      sendInt(frontLeftVal);
    } else if (request == 5) {
      sendInt(backRightVal);
    } else if (request == 6) {
      sendInt(backLeftVal);
    } else if (request == 7) {
      sendInt(backVal);
    } else if (request == 8) {
      sendInt(frontVal);
      sendInt(right45Val);
      sendInt(frontRightVal);
      sendInt(left45Val);
      sendInt(frontLeftVal);
      sendInt(backRightVal);
      sendInt(backLeftVal);
      sendInt(backVal);
    }

    digitalWrite(redLED, LOW);
    digitalWrite(blueLED, LOW);
    digitalWrite(greenLED, LOW);
    digitalWrite(25, HIGH);
  }
  return -1;
}

void sendInt(int sendInt) {
  short int split = sendInt;
  byte b1 = split >> 8;
  byte b2 = split;
  TOFBus.write(b1);
  TOFBus.write(b2);
}

void sendWireInt(int sendInt) {
  short int split = sendInt;
  byte b1 = split >> 8;
  byte b2 = split;
  Wire1.write(b1);
  Wire1.write(b2);
}

int recieveWireInt() {
  byte b1 = Wire1.read();
  byte b2 = Wire1.read();

  short int returnInt = b1;

  returnInt = returnInt << 8;
  returnInt += b2;

  return returnInt;
}
int recieveInt() {
  byte b1 = TOFBus.read();
  byte b2 = TOFBus.read();

  short int returnInt = b1;

  returnInt = returnInt << 8;
  returnInt += b2;

  return returnInt;
}

//TOF SENSORS BELOW
int readFront() {
  //Serial.print("Reading a measurement... ");
  digitalWrite(greenLED, HIGH);
  digitalWrite(blueLED, LOW);
  front.rangingTest(&frontMeas, false);  // pass in 'true' to get debug data printout!
  digitalWrite(greenLED, LOW);
  if (frontMeas.RangeStatus != 4) {  // phase failures have incorrect data
    // Serial.print("Distance (mm): "); Serial.println(frontMeas.RangeMilliMeter);

    if (frontMeas.RangeMilliMeter != 8191) {
      return frontMeas.RangeMilliMeter;
    } else {
      digitalWrite(redLED, HIGH);

      return -1;
    }
  } else {
    // Serial.println(" out of range ");
  }
  digitalWrite(redLED, HIGH);

  return -1;
}


int readRight45() {
  //Serial.print("Reading a measurement... ");
  digitalWrite(greenLED, HIGH);
  digitalWrite(blueLED, LOW);
  right45.rangingTest(&right45Meas, false);  // pass in 'true' to get debug data printout!
  digitalWrite(greenLED, LOW);
  if (right45Meas.RangeStatus != 4) {  // phase failures have incorrect data
    // Serial.print("Distance (mm): "); Serial.println(frontMeas.RangeMilliMeter);

    if (right45Meas.RangeMilliMeter != 8191) {
      return right45Meas.RangeMilliMeter;
    } else {
      digitalWrite(redLED, HIGH);

      return -1;
    }
  } else {
    //Serial.println(" out of range ");
  }
  digitalWrite(redLED, HIGH);

  return -1;
}

int readFrontRight() {
  //Serial.print("Reading a measurement... ");
  digitalWrite(greenLED, HIGH);
  digitalWrite(blueLED, LOW);
  frontRight.rangingTest(&frontRightMeas, false);  // pass in 'true' to get debug data printout!
  digitalWrite(greenLED, LOW);
  if (frontRightMeas.RangeStatus != 4) {  // phase failures have incorrect data
    // Serial.print("Distance (mm): "); Serial.println(frontMeas.RangeMilliMeter);

    if (frontRightMeas.RangeMilliMeter != 8191) {
      return frontRightMeas.RangeMilliMeter;
    } else {
      digitalWrite(redLED, HIGH);

      return -1;
    }
  } else {
    // Serial.println(" out of range ");
  }
  digitalWrite(redLED, HIGH);

  return -1;
}

int readLeft45() {
  //Serial.print("Reading a measurement... ");
  digitalWrite(greenLED, HIGH);
  digitalWrite(blueLED, LOW);
  left45.rangingTest(&left45Meas, false);  // pass in 'true' to get debug data printout!
  digitalWrite(greenLED, LOW);
  if (left45Meas.RangeStatus != 4) {  // phase failures have incorrect data
    // Serial.print("Distance (mm): "); Serial.println(frontMeas.RangeMilliMeter);

    if (left45Meas.RangeMilliMeter != 8191) {
      return left45Meas.RangeMilliMeter;
    } else {
      digitalWrite(redLED, HIGH);

      return -1;
    }
  } else {
    // Serial.println(" out of range ");
  }
  digitalWrite(redLED, HIGH);

  return -1;
}

int readFrontLeft() {
  //Serial.print("Reading a measurement... ");
  digitalWrite(greenLED, HIGH);
  digitalWrite(blueLED, LOW);
  frontLeft.rangingTest(&frontLeftMeas, false);  // pass in 'true' to get debug data printout!
  digitalWrite(greenLED, LOW);
  if (frontLeftMeas.RangeStatus != 4) {  // phase failures have incorrect data
    // Serial.print("Distance (mm): "); Serial.println(frontMeas.RangeMilliMeter);

    if (frontLeftMeas.RangeMilliMeter != 8191) {
      return frontLeftMeas.RangeMilliMeter;
    } else {
      digitalWrite(redLED, HIGH);

      return -1;
    }
  } else {
    // Serial.println(" out of range ");
  }
  digitalWrite(redLED, HIGH);

  return -1;
}

int readBackLeft() {
  //Serial.print("Reading a measurement... ");
  digitalWrite(greenLED, HIGH);
  digitalWrite(blueLED, LOW);
  backLeft.rangingTest(&backLeftMeas, false);  // pass in 'true' to get debug data printout!
  digitalWrite(greenLED, LOW);
  if (backLeftMeas.RangeStatus != 4) {  // phase failures have incorrect data
    // Serial.print("Distance (mm): "); Serial.println(frontMeas.RangeMilliMeter);

    if (backLeftMeas.RangeMilliMeter != 8191) {
      return backLeftMeas.RangeMilliMeter;
    } else {
      digitalWrite(redLED, HIGH);

      return -1;
    }
  } else {
    // Serial.println(" out of range ");
  }
  digitalWrite(redLED, HIGH);

  return -1;
}

int readBackRight() {
  //Serial.print("Reading a measurement... ");
  digitalWrite(greenLED, HIGH);
  digitalWrite(blueLED, LOW);
  backRight.rangingTest(&backRightMeas, false);  // pass in 'true' to get debug data printout!
  digitalWrite(greenLED, LOW);
  if (backRightMeas.RangeStatus != 4) {  // phase failures have incorrect data
    // Serial.print("Distance (mm): "); Serial.println(frontMeas.RangeMilliMeter);

    if (backRightMeas.RangeMilliMeter != 8191) {
      return backRightMeas.RangeMilliMeter;
    } else {
      digitalWrite(redLED, HIGH);

      return -1;
    }
  } else {
    // Serial.println(" out of range ");
  }
  digitalWrite(redLED, HIGH);

  return -1;
}

int readBack() {
  //Serial.print("Reading a measurement... ");
  digitalWrite(greenLED, HIGH);
  digitalWrite(blueLED, LOW);
  back.rangingTest(&backMeas, false);  // pass in 'true' to get debug data printout!
  digitalWrite(greenLED, LOW);
  if (backMeas.RangeStatus != 4) {  // phase failures have incorrect data
    // Serial.print("Distance (mm): "); Serial.println(frontMeas.RangeMilliMeter);

    if (backMeas.RangeMilliMeter < 2500) {
      return backMeas.RangeMilliMeter;
    } else {
      digitalWrite(redLED, HIGH);

      return -1;
    }
  } else {
    // Serial.println(" out of range ");
  }
  digitalWrite(redLED, HIGH);

  return -1;
}
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

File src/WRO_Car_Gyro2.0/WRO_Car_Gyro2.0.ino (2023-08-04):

#include <BMI160Gen.h>
#include <SoftwareSerial.h>

#include <Servo.h>

#include <Wire.h>

Servo myservo;
const int select_pin = 10;
const int i2c_addr = 0x69;

const int servoPin = 2;



int targetAngle = 0;



int angle = 0;
//top top left mid bottomleft bottom dot bottomright topright
int seg1[] = { 15, 14, 13, 12, 11, 10, 9, 8 };

int seg2[] = { 21, 17, 6, 16, 27, 20, 3, 7 };

const int redLED = 12;
const int greenLED = 11;


SoftwareSerial comBus(8, 9);  // RX, TX

long int oldTime = 0;
long int gyroValue = 0;
float gyroOfset = -20.79;

int angleOld = -100;


void setup() {

  pinMode(25, OUTPUT);
  digitalWrite(25, HIGH);
  delay(100);
  digitalWrite(25, LOW);
  delay(100);
  digitalWrite(25, HIGH);

  initSegs();


 




  //comBus.begin(57600);

  Serial.println("FLASH");

  bootAimation();
  Wire1.setSDA(18);
  Wire1.setSCL(19);
  Serial.println("Wire1 SET");
  Wire1.begin(12);
  Serial.println("wire1 BEGIN");



  
  Serial.println("FLASH");
  myservo.attach(servoPin);
  Serial.println("Servo attached");
bootAimation();

  Wire1.onReceive(receiveEvent);  // register event
  Wire1.onRequest(requestEvent);
  Serial.println("Func set");

  


  Serial.println("Serial begun");


  // initialize device


  Serial.println("Init gyro");
  if (!(BMI160.begin(BMI160GenClass::I2C_MODE, i2c_addr))) {
    while (1) {
      Serial.println("Failed to initialise");
      delay(1000);
    }
  }
  Serial.println("Initialised");
 updateSeg1('C');
  calibrateGyro();
  bootAimation();
  oldTime = millis();

  for (int i = 0; i < 10; i++) {

    updateSeg1(i);
    updateSeg2(i);
    delay(100);
  }

  updateSeg1(0);
  updateSeg2(0);
}

void loop() {

  steer();




  integrateZ();
}


void steer() {

  angle = gyroValue / 130000;  //checkGyro();

  
  if(angleOld != angle){

    updateSeg1(abs((angle%100)/10));
    updateSeg2(abs(angle%10));
    angleOld = angle;
  }


  int angleDiff = targetAngle + angle;
  Serial.print("TRUE ANGLE- ");
  Serial.print(angle);
    Serial.print("\tAngle diff -- ");
  Serial.print(angleDiff);
  Serial.print("\tTarget Angle - ");
  Serial.print(targetAngle);
  int maxSteering = 30;
  if (angleDiff > maxSteering) {
    angleDiff = maxSteering;
  } else if (angleDiff < -maxSteering) {
    angleDiff = -maxSteering;
  }

  int steeringAngle = angleDiff * 3 + 103;
  Serial.print("\tSteering angle - ");
  Serial.println(steeringAngle);
  myservo.write(steeringAngle);
}

int recieveInt() {
  byte b1 = Wire1.read();
  byte b2 = Wire1.read();

  int returnInt = b1;

  returnInt = returnInt << 8;
  returnInt += b2;

  return returnInt;
}
void sendInt(int sendInt) {
  byte b1 = sendInt >> 8;
  byte b2 = sendInt;
  Wire1.write(b1);
  Wire1.write(b2);
}
int checkSerial() {

  if (comBus.available() > 0) {


    int code = comBus.read();


    Serial.println(code);
    return code;
  }

  return -1;
}

void integrateZ() {


  long int newTime = millis();


  int gx, gy, gz;  // raw gyro values

  // read raw gyro measurements from device
  BMI160.readGyro(gx, gy, gz);

  // display tab-separated gyro x/y/z values

  

  gyroValue += (gz - gyroOfset) * (newTime - oldTime);
  oldTime = newTime;
}



void calibrateGyro() {


  long int totalDrift = 0;

  for (int i = 0; i < 1000; i++) {


    int gx, gy, gz;  // raw gyro values

    // read raw gyro measurements from device
    BMI160.readGyro(gx, gy, gz);
    Serial.println(i);
    totalDrift += gz;
  }

  gyroOfset = totalDrift / 1000.0;

  Serial.println("Gyro Offset");
  Serial.println(gyroOfset);
  delay(1000);
}


void receiveEvent(int len) {
updateSeg1('.');
updateSeg2('.');

  int16_t tatmp = recieveInt();
   targetAngle = tatmp;
  delay(5);
  Serial.print("RECIEVED\t\t\t\t Target angle  =");
  Serial.println(targetAngle);
  //int motor = Wire.read();
  //delay(1000);
}

void requestEvent() {

  sendInt(angle);
}



void bootAimation() {

  for (int i = 0; i < 8; i++) {
    Serial.println(i);
    digitalWrite(seg1[i], LOW);
    delay(50);
    digitalWrite(seg1[i], HIGH);
  }

  for (int i = 0; i < 8; i++) {
    Serial.println(seg2[i]);
    digitalWrite(seg2[i], LOW);
    delay(50);
    digitalWrite(seg2[i], HIGH);
  }
}



void updateSeg1(char displayNum) {
  for (int i = 0; i < 8; i++) {
    digitalWrite(seg1[i], HIGH);
  }

  if (displayNum == 0) {
    digitalWrite(seg1[0], LOW);
    digitalWrite(seg1[1], LOW);
    digitalWrite(seg1[7], LOW);
    digitalWrite(seg1[3], LOW);
    digitalWrite(seg1[4], LOW);
    digitalWrite(seg1[6], LOW);
  } else if (displayNum == 1) {
    digitalWrite(seg1[6], LOW);
    digitalWrite(seg1[7], LOW);
  } else if (displayNum == 2) {
    digitalWrite(seg1[0], LOW);
    digitalWrite(seg1[7], LOW);
    digitalWrite(seg1[2], LOW);
    digitalWrite(seg1[3], LOW);
    digitalWrite(seg1[4], LOW);
  } else if (displayNum == 3) {
    digitalWrite(seg1[0], LOW);
    digitalWrite(seg1[7], LOW);
    digitalWrite(seg1[2], LOW);
    digitalWrite(seg1[6], LOW);
    digitalWrite(seg1[4], LOW);
  } else if (displayNum == 4) {
    digitalWrite(seg1[1], LOW);
    digitalWrite(seg1[7], LOW);
    digitalWrite(seg1[2], LOW);
    digitalWrite(seg1[6], LOW);
  } else if (displayNum == 5) {
    digitalWrite(seg1[0], LOW);
    digitalWrite(seg1[1], LOW);
    digitalWrite(seg1[2], LOW);
    digitalWrite(seg1[6], LOW);
    digitalWrite(seg1[4], LOW);
  } else if (displayNum == 6) {
    digitalWrite(seg1[0], LOW);
    digitalWrite(seg1[1], LOW);
    digitalWrite(seg1[2], LOW);
    digitalWrite(seg1[3], LOW);
    digitalWrite(seg1[6], LOW);
    digitalWrite(seg1[4], LOW);
  } else if (displayNum == 7) {
    digitalWrite(seg1[0], LOW);
    digitalWrite(seg1[7], LOW);
    digitalWrite(seg1[6], LOW);
  } else if (displayNum == 8) {
    digitalWrite(seg1[0], LOW);
    digitalWrite(seg1[1], LOW);
    digitalWrite(seg1[2], LOW);
    digitalWrite(seg1[3], LOW);
    digitalWrite(seg1[4], LOW);
    digitalWrite(seg1[6], LOW);
    digitalWrite(seg1[7], LOW);
  } else if (displayNum == 9) {
    digitalWrite(seg1[0], LOW);
    digitalWrite(seg1[1], LOW);
    digitalWrite(seg1[2], LOW);
    digitalWrite(seg1[7], LOW);
    digitalWrite(seg1[6], LOW);
  } else if (displayNum == 'C') {
    digitalWrite(seg1[0], LOW);
    digitalWrite(seg1[1], LOW);
    digitalWrite(seg1[3], LOW);
    digitalWrite(seg1[4], LOW);
 
 } else if (displayNum == 'F') {
    digitalWrite(seg1[0], LOW);
    digitalWrite(seg1[1], LOW);
    digitalWrite(seg1[3], LOW);
    digitalWrite(seg1[2], LOW);
 } else if (displayNum == '.') {
    digitalWrite(seg1[5], LOW);
  }  
}
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

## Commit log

2023-03-04 changed fc to relay
2023-03-18 Camera ESp 32
2023-03-27 Installed ESP-32CAM libary
    Installed the libaries that should contain the ESP 32 CAM. For whatever reason, I cannot find this device.
2023-04-12 Camera stuff
2023-07-23 motor controller
2023-08-05 3D model
    [body_v2.stl]
